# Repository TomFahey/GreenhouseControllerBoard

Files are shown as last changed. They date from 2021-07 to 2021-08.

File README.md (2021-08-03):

# Greenhouse Controller Board
Greenhouse irrigation control and sensor board, based on the ESP32 microcontroller and designed with Autodesk Eagle.

A simple 2-layer PCB design for an irrigation controller, designed to control up to four 12V solenoid valve water valves, 
based on temperature, humidity and other arbitrary parameters.

Based on Espressif's popular ESP32 microncontroller, this controller board incorporates a number of features, including:

- Flexible Wi-Fi/Bluetooth control, tracking and automation of plants through open-source Arduino libraries (also compatible with ESPHome)
- Individual control for up to four DC solenoid valves via 2.1mm x 5.5mm barrel jack, with LED status indicators
- 12V DC power input, built-in 3.3V voltage regulation for microcontroller and peripherals, up to 4A load
- High precision temperature, pressure and humidity sensing, using Bosch's BME280 MEMS sensor
- Up to 8 individual 12-bit ADC channels for additional environmental monitoring, such as soil moisture sensors
- An additional 4 GPIO channels, and two I2C connectors for further expansion e.g LED strips (separate power supply required)

Some renders from Fusion 360:

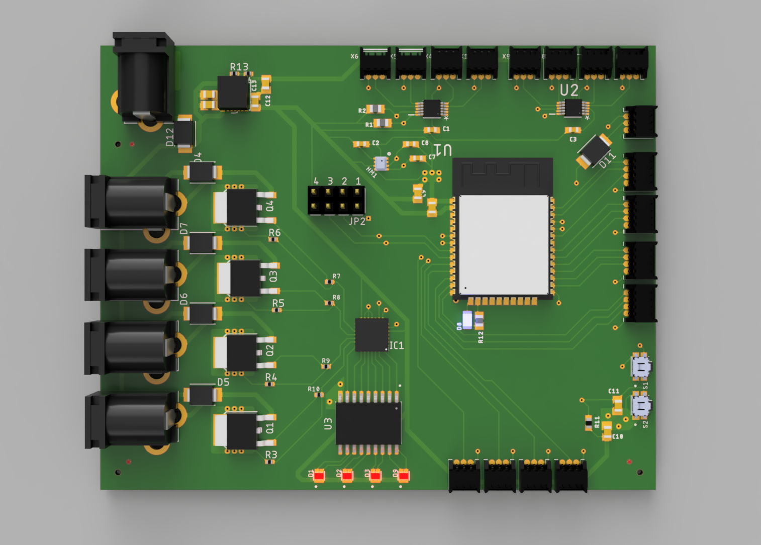
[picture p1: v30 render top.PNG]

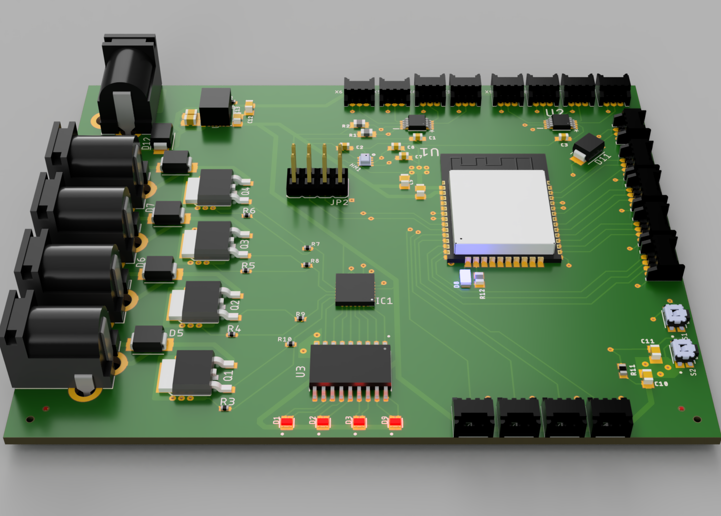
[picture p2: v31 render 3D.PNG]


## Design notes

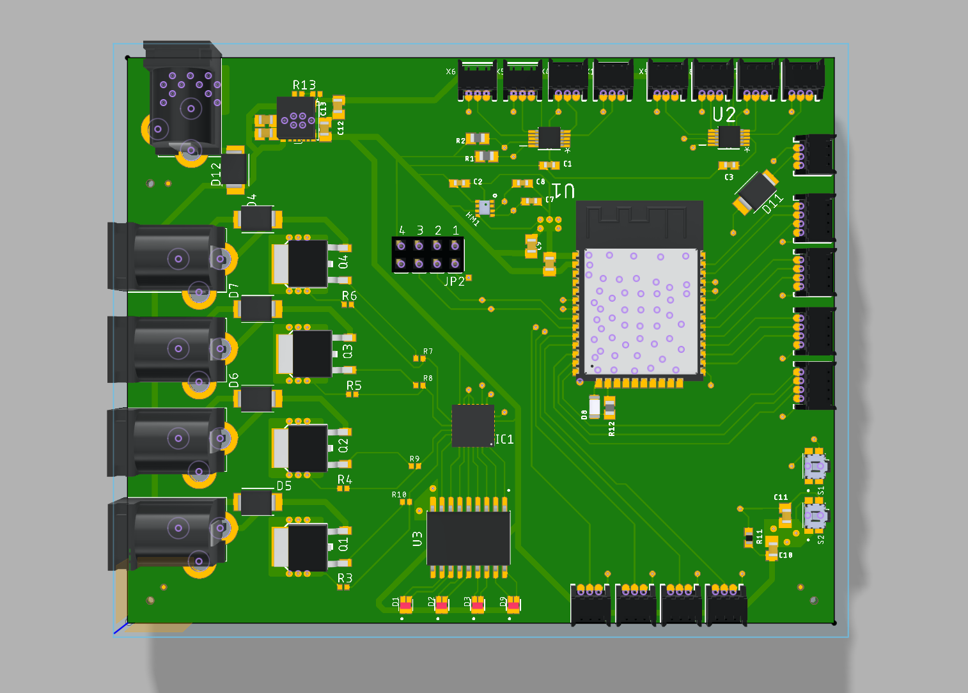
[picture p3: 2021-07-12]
v31 CAD top.png

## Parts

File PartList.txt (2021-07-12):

Partlist

Exported from Controller v2.sch at 12/07/2021 17:28

EAGLE Version 9.6.2 Copyright (c) 1988-2020 Autodesk, Inc.

Assembly variant: 

Part      Value               Device              Package              Library                                Sheet

12V_OUT_A 2.1MMJACKTHM        2.1MMJACKTHM        PJ-102A              adafruit                               1
12V_OUT_B 2.1MMJACKTHM        2.1MMJACKTHM        PJ-102A              adafruit                               1
12V_OUT_C 2.1MMJACKTHM        2.1MMJACKTHM        PJ-102A              adafruit                               1
12V_OUT_D 2.1MMJACKTHM        2.1MMJACKTHM        PJ-102A              adafruit                               1
C1        0.1uF               C-EUC0603           C0603                rcl                                    1
C2        50nF                C-EUC0603           C0603                rcl                                    1
C3        0.1uF               C-EUC0603           C0603                rcl                                    1
C4        10uF                C-EUC0805K          C0805K               rcl                                    1
C5        10uF                C-EUC0805K          C0805K               rcl                                    1
C6        10uF                C-EUC0805K          C0805K               rcl                                    1
C7        135pF               C-EUC0603           C0603                rcl                                    1
C8        135pF               C-EUC0603           C0603                rcl                                    1
C9        10uF                C-EUC0805K          C0805K               rcl                                    1
C10       10uF                C-EUC0805K          C0805K               rcl                                    1
C11       1uF                 C-EUC0805K          C0805K               rcl                                    1
C12       47uF                C-EUC0805K          C0805K               rcl                                    1
C13       47uF                C-EUC0805K          C0805K               rcl                                    1
D1        LTST-C195TBJRKT0605 LTST-C195TBJRKT0605 LED_LTST-C195TBJRKT  LTST-C195TBJRKT                        1
D2        LTST-C195TBJRKT0605 LTST-C195TBJRKT0605 LED_LTST-C195TBJRKT  LTST-C195TBJRKT                        1
D3        LTST-C195TBJRKT0605 LTST-C195TBJRKT0605 LED_LTST-C195TBJRKT  LTST-C195TBJRKT                        1
D4        ES2D                ES2D                SMB                  diode                                  1
D5        ES2D                ES2D                SMB                  diode                                  1
D6        ES2D                ES2D                SMB                  diode                                  1
D7        ES2D                ES2D                SMB                  diode                                  1
D8        RED                 LEDCHIPLED_0805     CHIPLED_0805         adafruit                               1
D9        LTST-C195TBJRKT0605 LTST-C195TBJRKT0605 LED_LTST-C195TBJRKT  LTST-C195TBJRKT                        1
D11       ES2D                ES2D                SMB                  diode                                  1
D12       ES2D                ES2D                SMB                  diode                                  1
HM1       BME2808-VFLGA       BME2808-VFLGA       BME280               SamacSys_Parts                         1
IC1       MCP23017ML          MCP23017ML          QFN28-ML_6X6MM       microchip                              1
JP2       3.3V                JP4QE               JP4Q                 jumper                                 1
PWRIN     2.1MMJACKTHM        2.1MMJACKTHM        PJ-102A              adafruit                               1
Q1        AOD4184A            AOD4184A            D-PAK_TO252AA        AOD4184A                               1
Q2        AOD4184A            AOD4184A            D-PAK_TO252AA        AOD4184A                               1
Q3        AOD4184A            AOD4184A            D-PAK_TO252AA        AOD4184A                               1
Q4        AOD4184A            AOD4184A            D-PAK_TO252AA        AOD4184A                               1
R1        4.7K                R-EU_R0805          R0805                rcl                                    1
R2        4.7K                R-EU_R0805          R0805                rcl                                    1
R3        100                 R-EU_R0402          R0402                rcl                                    1
R4        100                 R-EU_R0402          R0402                rcl                                    1
R5        100                 R-EU_R0402          R0402                rcl                                    1
R6        100                 R-EU_R0402          R0402                rcl                                    1
R7        1K                  R-EU_R0402          R0402                rcl                                    1
R8        1K                  R-EU_R0402          R0402                rcl                                    1
R9        1K                  R-EU_R0402          R0402                rcl                                    1
R10       1K                  R-EU_R0402          R0402                rcl                                    1
R11       10K                 R-EU_R0603          R0603                rcl                                    1
R12       10K                 R-EU_R0805          R0805                rcl                                    1
R13       4.32K               R-EU_R0402          R0402                rcl                                    1
R14       10K                 R-EU_R0402          R0402                rcl                                    1
S1        EVQ-P7L01P          EVQ-P7L01P          SW_EVQ-P7L01P        EVQ-P7L01P                             1
S2        EVQ-P7L01P          EVQ-P7L01P          SW_EVQ-P7L01P        EVQ-P7L01P                             1
U1        ADS1115IDGST        ADS1115IDGST        SOP50P490X110-10N    Texas Instruments_By_element14_Batch_1 1
U2        ADS1115IDGST        ADS1115IDGST        SOP50P490X110-10N    Texas Instruments_By_element14_Batch_1 1
U3        ULN2803ADWRG4       ULN2803ADWRG4       SOIC127P1030X265-18N ULN2803ADWRG4                          1
U4        TPSM53604RDAR       TPSM53604RDAR       B3QFN14_RDA_TEX      TPSM53604                              1
X1        53048-03            53048-03            53048-03             con-molex                              1
X2        ESP32_WROOM32       ESP32_WROOM32       WROOM32              microbuilder                           1
X3        53048-03            53048-03            53048-03             con-molex                              1
X4        53048-03            53048-03            53048-03             con-molex                              1
X5        53048-03            53048-03            53048-03             con-molex                              1
X6        53048-03            53048-03            53048-03             con-molex                              1
X7        53048-03            53048-03            53048-03             con-molex                              1
X8        53048-03            53048-03            53048-03             con-molex                              1
X9        53048-03            53048-03            53048-03             con-molex                              1
X10       53048-04            53048-04            53048-04             con-molex                              1
X11       53048-04            53048-04            53048-04             con-molex                              1
X12       53048-04            53048-04            53048-04             con-molex                              1
X13       53048-03            53048-03            53048-03             con-molex                              1
X14       53048-04            53048-04            53048-04             con-molex                              1
X15       53048-03            53048-03            53048-03             con-molex                              1
X16       53048-03            53048-03            53048-03             con-molex                              1
X17       53048-03            53048-03            53048-03             con-molex                              1
X18       53048-03            53048-03            53048-03             con-molex                              1

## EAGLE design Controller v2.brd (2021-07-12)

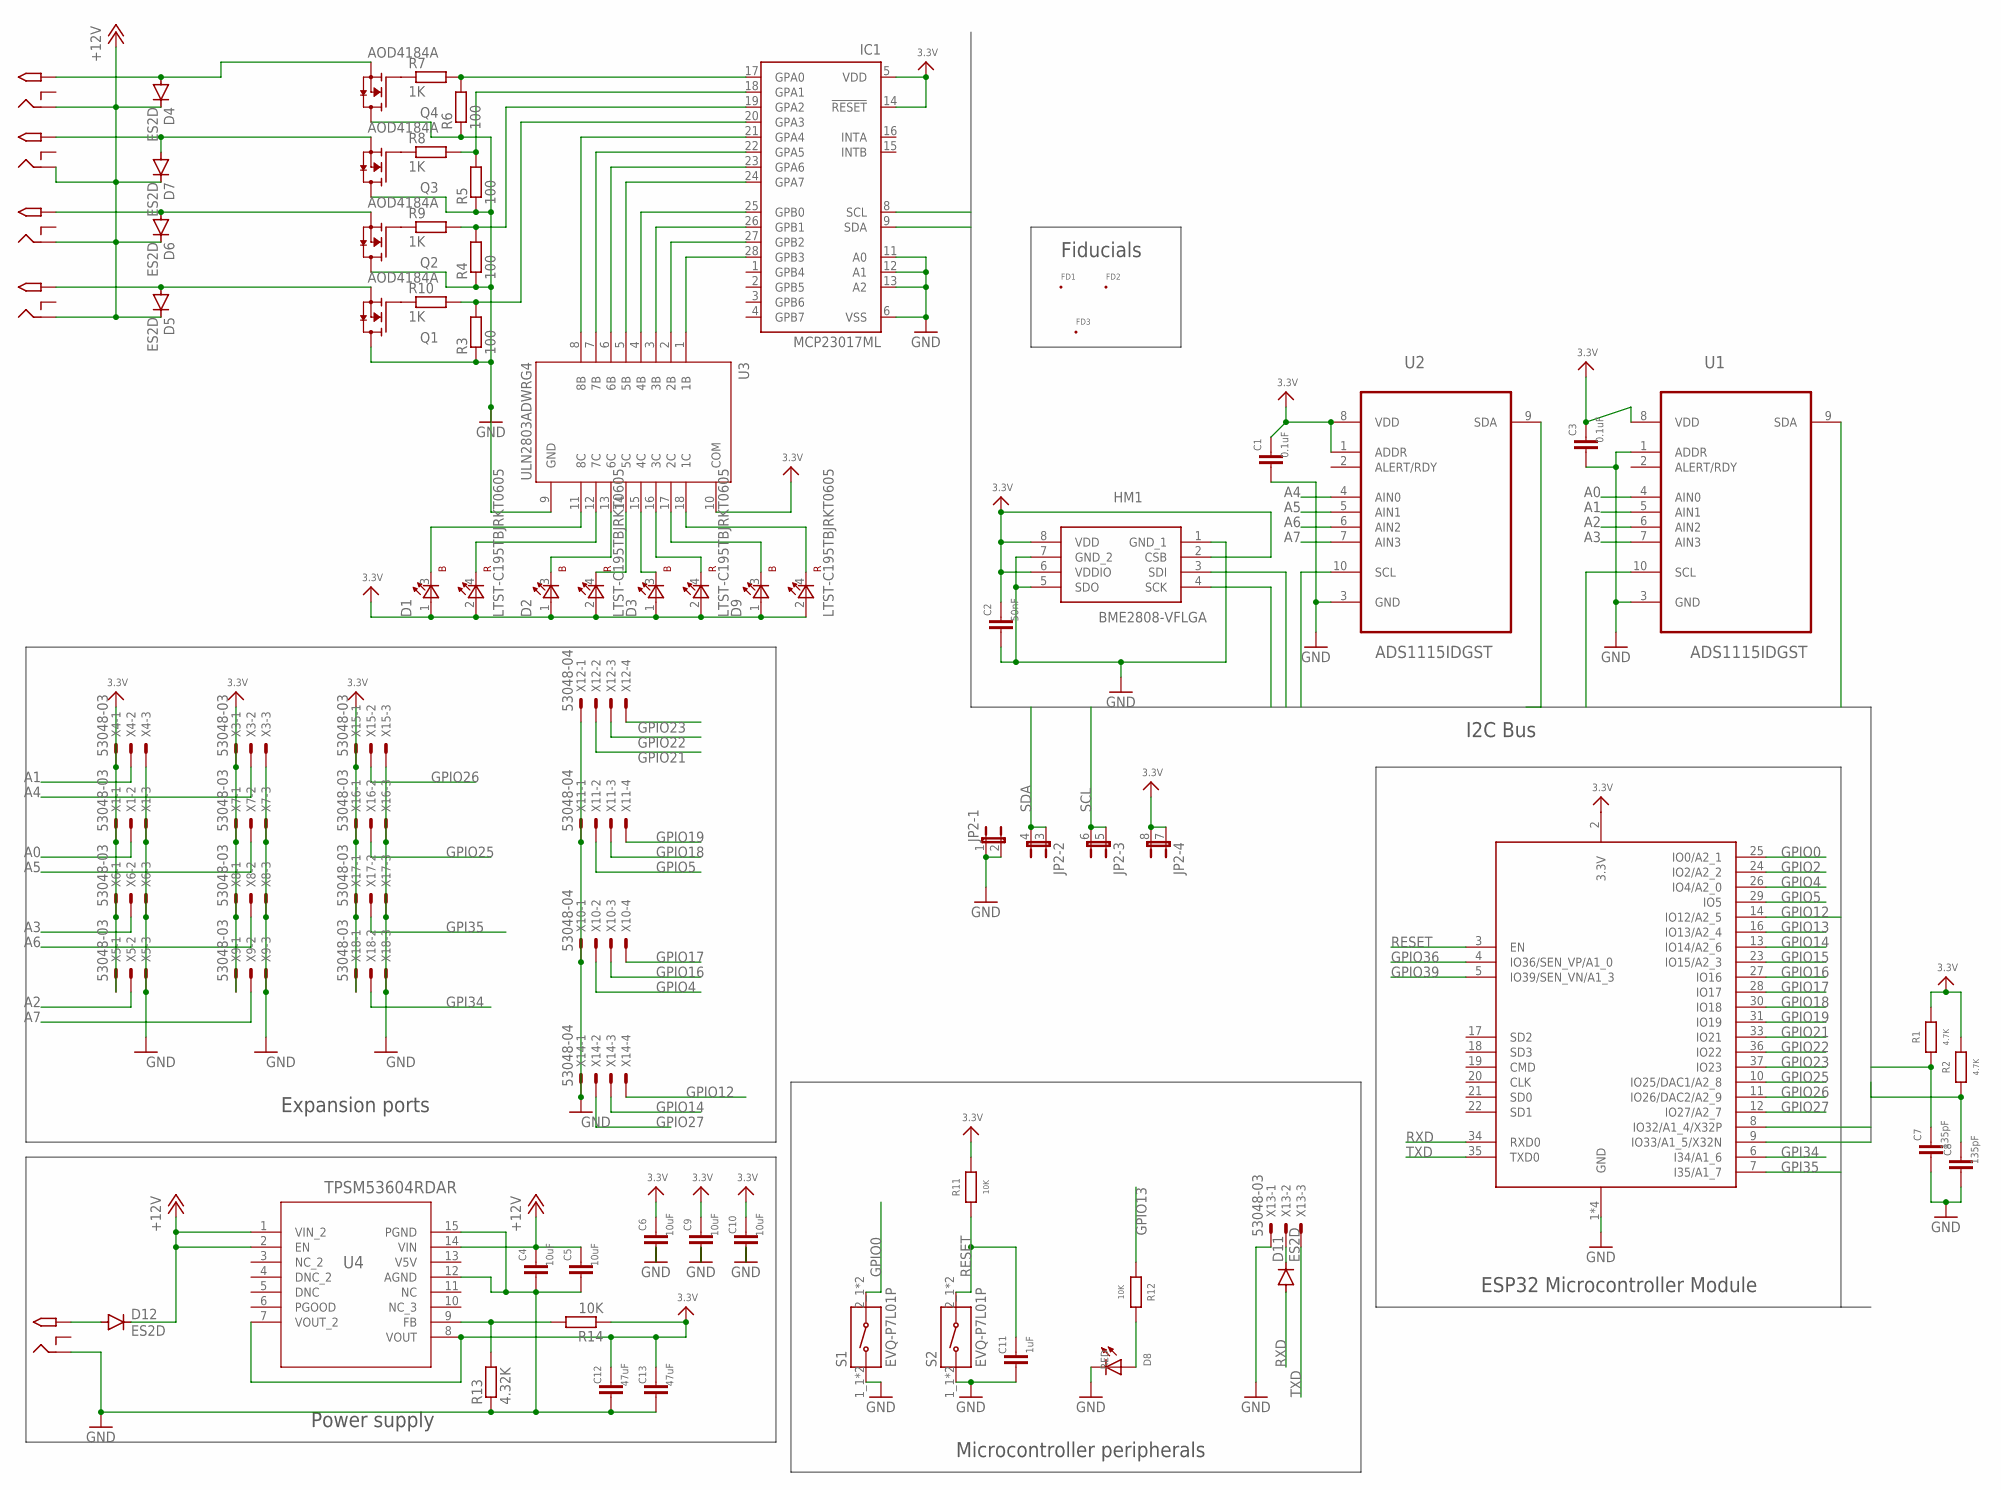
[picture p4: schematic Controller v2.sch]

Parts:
12V_OUT_A, 12V_OUT_B, 12V_OUT_C, 12V_OUT_D: 2.1MMJACKTHM; PJ-102A
C1, C3: 0.1uF; C0603
C2: 50nF; C0603
C4, C5, C6, C9, C10: 10uF; C0805K
C7, C8: 135pF; C0603
C11: 1uF; C0805K
C12, C13: 47uF; C0805K
D1, D2, D3, D9: LTST-C195TBJRKT0605; LED_LTST-C195TBJRKT
D4, D5, D6, D7, D11, D12: ES2D; SMB; MPN ES2D; DIGI-KEY-PART-NUMBER ES2DFSCT-ND
D8: RED; CHIPLED_0805
FD1, FD2, FD3: FID_20MIL; FID_020
HM1: BME2808-VFLGA; BME280
IC1: MCP23017ML; QFN28-ML_6X6MM
JP2: 3.3V; JP4Q
PWRIN: 2.1MMJACKTHM; PJ-102A
Q1, Q2, Q3, Q4: AOD4184A; D-PAK_TO252AA
R1, R2: 4.7K; R0805
R3, R4, R5, R6: 100; R0402
R7, R8, R9, R10: 1K; R0402
R11: 10K; R0603
R12: 10K; R0805
R13: 4.32K; R0402
R14: 10K; R0402
S1, S2: EVQ-P7L01P; SW_EVQ-P7L01P
U1, U2: ADS1115IDGST; SOP50P490X110-10N
U3: ULN2803ADWRG4; SOIC127P1030X265-18N
U4: TPSM53604RDAR; B3QFN14_RDA_TEX
X1, X3, X4, X5, X6, X7, X8, X9, X13, X15, X16, X17, X18: 53048-03
X2: ESP32_WROOM32; WROOM32; MPN N/A
X10, X11, X12, X14: 53048-04

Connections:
3.3V: C1.1, C2.1, C3.1, C6.1, C9.1, C10.1, C12.1, C13.1, D1.1 (A1), D1.2 (A2), D2.1 (A1), D2.2 (A2), D3.1 (A1), D3.2 (A2), D9.1 (A1), D9.2 (A2), HM1.2 (CSB), HM1.6 (VDDIO), HM1.8 (VDD), IC1.5 (VDD), IC1.14 (!RESET), JP2.7 (1), JP2.8 (2), R1.2, R2.2, R11.2, R14.1, U1.8 (VDD), U2.1 (ADDR), U2.8 (VDD), U3.10 (COM), U4.7 (VOUT_2), U4.8 (VOUT), X1.1, X2.2 (3.3V), X3.1, X4.1, X5.1, X6.1, X7.1, X8.1, X9.1, X15.1, X16.1, X17.1, X18.1
+12V: 12V_OUT_A.RING, 12V_OUT_B.RING, 12V_OUT_C.RING, 12V_OUT_D.RING, C4.1, C5.1, D4.C, D5.C, D6.C, D7.C, D12.C, U4.1 (VIN_2), U4.2 (EN), U4.14 (VIN)
A0: U1.4 (AIN0), X1.2
A1: U1.5 (AIN1), X4.2
A2: U1.6 (AIN2), X5.2
A3: U1.7 (AIN3), X6.2
A4: U2.4 (AIN0), X3.2
A5: U2.5 (AIN1), X7.2
A6: U2.6 (AIN2), X8.2
A7: U2.7 (AIN3), X9.2
GND: C1.2, C2.2, C3.2, C4.2, C5.2, C6.2, C7.2, C8.2, C9.2, C10.2, C11.2, C12.2, C13.2, D8.C, HM1.1 (GND_1), HM1.5 (SDO), HM1.7 (GND_2), IC1.6 (VSS), IC1.11 (A0), IC1.12 (A1), IC1.13 (A2), JP2.1, JP2.2, PWRIN.RING, Q1.4 (D), Q2.4 (D), Q3.4 (D), Q4.4 (D), R3.1, R4.1, R5.1, R6.1, R13.1, S1.1_1 (1), S1.1_2 (1), S2.1_1 (1), S2.1_2 (1), U1.1 (ADDR), U1.3 (GND), U2.3 (GND), U3.9 (GND), U4.12 (AGND), U4.15 (PGND), X1.3, X2.1 (GND), X2.15 (GND), X2.38 (GND), X2.P$1 (GND), X3.3, X4.3, X5.3, X6.3, X7.3, X8.3, X9.3, X10.1, X11.1, X12.1, X13.1, X14.1, X15.3, X16.3, X17.3, X18.3
GPI34: X2.6 (I34/A1_6), X18.2
GPI35: X2.7 (I35/A1_7), X17.2
GPIO0: S1.2_1 (2), S1.2_2 (2), X2.25 (IO0/A2_1)
GPIO2: X2.24 (IO2/A2_2)
GPIO4: X2.26 (IO4/A2_0), X10.2
GPIO5: X2.29 (IO5), X11.2
GPIO12: X2.14 (IO12/A2_5), X14.4
GPIO13: R12.1, X2.16 (IO13/A2_4)
GPIO14: X2.13 (IO14/A2_6), X14.3
GPIO15: X2.23 (IO15/A2_3)
GPIO16: X2.27 (IO16), X10.3
GPIO17: X2.28 (IO17), X10.4
GPIO18: X2.30 (IO18), X11.3
GPIO19: X2.31 (IO19), X11.4
GPIO21: X2.33 (IO21), X12.2
GPIO22: X2.36 (IO22), X12.3
GPIO23: X2.37 (IO23), X12.4
GPIO25: X2.10 (IO25/DAC1/A2_8), X16.2
GPIO26: X2.11 (IO26/DAC2/A2_9), X15.2
GPIO27: X2.12 (IO27/A2_7), X14.2
GPIO36: X2.4 (IO36/SEN_VP/A1_0)
GPIO39: X2.5 (IO39/SEN_VN/A1_3)
unnamed: IC1.17 (GPA0), R6.2, R7.2
unnamed: IC1.18 (GPA1), R5.2, R8.2
unnamed: IC1.20 (GPA3), R3.2, R10.2
unnamed: IC1.19 (GPA2), R4.2, R9.2
unnamed: Q1.1 (G), R10.1
unnamed: D12.A, PWRIN.TIP
unnamed: Q2.1 (G), R9.1
unnamed: IC1.21 (GPA4), U3.8 (8B)
unnamed: Q3.1 (G), R8.1
unnamed: Q4.1 (G), R7.1
unnamed: D11.C, X13.2
unnamed: IC1.22 (GPA5), U3.7 (7B)
unnamed: IC1.23 (GPA6), U3.6 (6B)
unnamed: IC1.24 (GPA7), U3.5 (5B)
unnamed: D8.A, R12.2
unnamed: IC1.25 (GPB0), U3.4 (4B)
unnamed: IC1.26 (GPB1), U3.3 (3B)
unnamed: IC1.27 (GPB2), U3.2 (2B)
unnamed: IC1.28 (GPB3), U3.1 (1B)
unnamed: D1.3 (K1), U3.11 (8C)
unnamed: D1.4 (K2), U3.12 (7C)
unnamed: D2.3 (K1), U3.13 (6C)
unnamed: D2.4 (K2), U3.14 (5C)
unnamed: D3.3 (K1), U3.15 (4C)
unnamed: D3.4 (K2), U3.16 (3C)
unnamed: D9.3 (K1), U3.17 (2C)
unnamed: D9.4 (K2), U3.18 (1C)
unnamed: R13.2, R14.2, U4.9 (FB)
RESET: C11.1, R11.1, S2.2_1 (2), S2.2_2 (2), X2.3 (EN)
RXD: D11.A, X2.34 (RXD0)
SCL: C7.1, HM1.4 (SCK), IC1.8 (SCL), JP2.5 (1), JP2.6 (2), R1.1, U1.10 (SCL), U2.10 (SCL), X2.9 (IO33/A1_5/X32N)
SDA: C8.1, HM1.3 (SDI), IC1.9 (SDA), JP2.3 (1), JP2.4 (2), R2.1, U1.9 (SDA), U2.9 (SDA), X2.8 (IO32/A1_4/X32P)
TXD: X2.35 (TXD0), X13.3
V_COL1: 12V_OUT_A.TIP, D4.A, Q4.3 (S)
V_COL2: 12V_OUT_B.TIP, D7.A, Q3.3 (S)
V_COL3: 12V_OUT_C.TIP, D6.A, Q2.3 (S)
V_COL4: 12V_OUT_D.TIP, D5.A, Q1.3 (S)

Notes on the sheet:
Fiducials
I2C Bus
Microcontroller peripherals
ESP32 Microcontroller Module
Power supply
Expansion ports

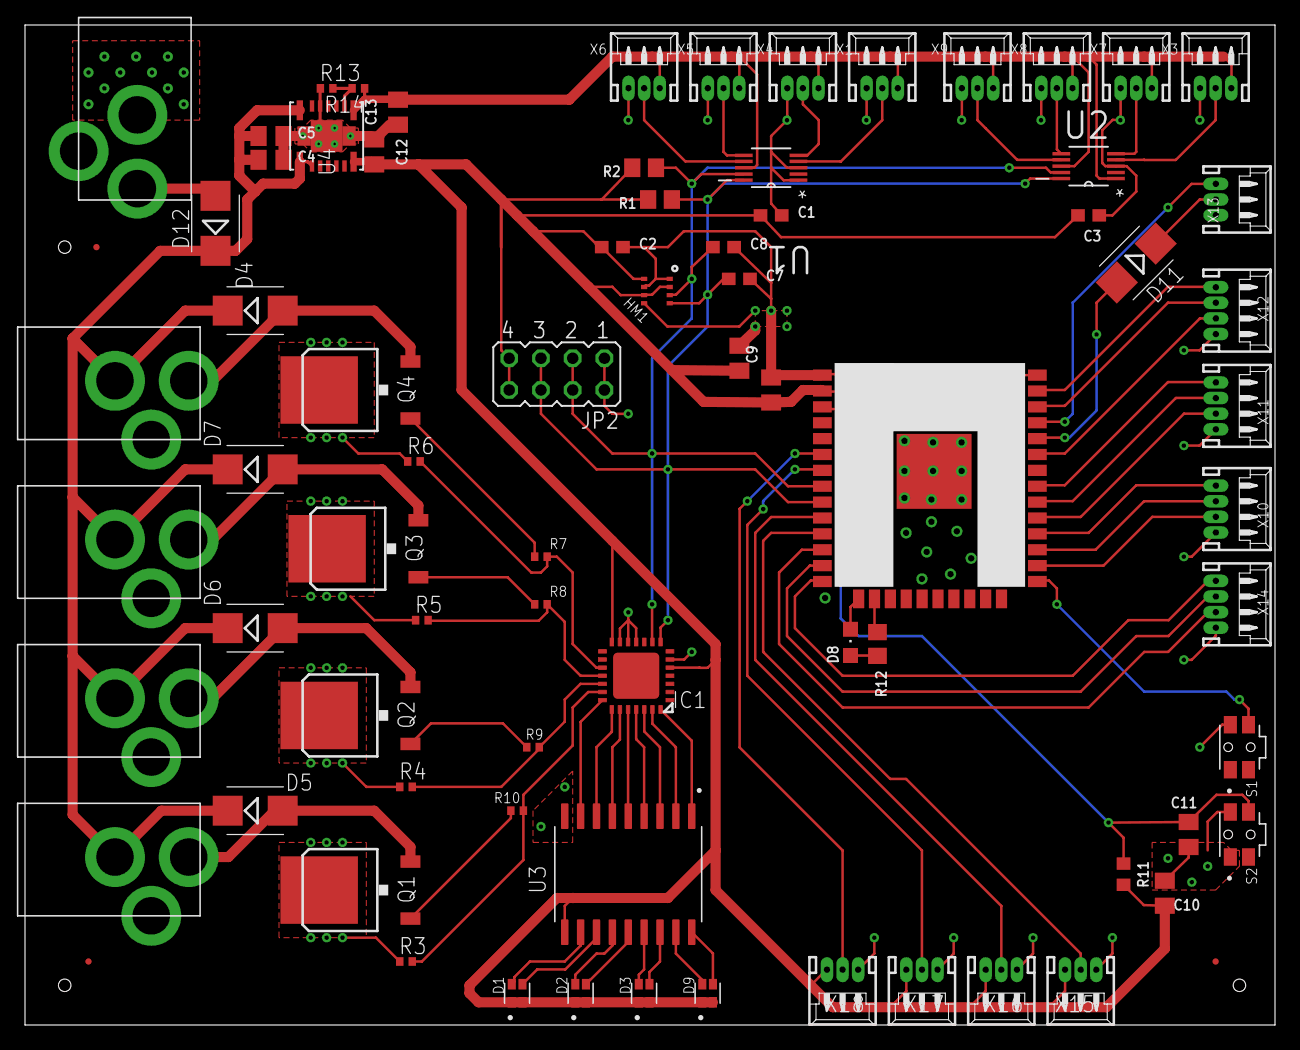
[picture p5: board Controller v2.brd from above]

Board: 2 copper layers, 100.0 x 80.0 mm, 77 parts (0 on the bottom side), 66 nets.

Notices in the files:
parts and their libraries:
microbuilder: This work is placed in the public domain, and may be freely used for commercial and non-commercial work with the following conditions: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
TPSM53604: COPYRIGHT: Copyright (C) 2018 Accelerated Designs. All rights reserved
